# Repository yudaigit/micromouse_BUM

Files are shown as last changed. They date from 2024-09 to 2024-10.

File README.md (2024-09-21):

# Micromouse "BUM"
Contains micromouse specification, code, and list of items.

# Table of Contents
1. Introduction
2. Design Goals
3. Schematic diagram
4. Parts List
5. Codes

# 1. Introduction
**Micromouse** : A maze-solving robot with wall sensors and electric motor.

**Expected specification of this mouse**
- Motor: Stepping Motor (for ease of coding)
- Microcontroller: ESP32
- Wall detection: IR LED + suitable phototransistor
- Wheels: 2 wheels + sheet with smooth surface in front
- Battery: Lipo battery (12V)
- Maze-solving algorism Adachi method
- Chassis would be made out of circuit board. 

**Important Regulation** 
- Mouse must fit on 18cm x 18cm unit square.
- Each run that in which the mouse successfully reaches the goal is given a run time.
- Shortest time out of all runs is considered the official record. 
- 10 minutes limit including adjusting parameters.
- No limit on the number of runs
Regulation found here [2024 IEEE MIT Micromouse Guideline.pdf](https://github.com/user-attachments/files/17085412/2024.IEEE.MIT.Micromouse.Guideline.pdf)

Micromouse_maze
Picture from Wikipedia [Link](https://en.wikipedia.org/wiki/Micromouse)

# 2. Design Goals
Design of this mouse is referred to Beginner Mouse V2 by Micromouse Hokuriku Dokokai. 

Website Link: [Click here](https://sites.google.com/a/itolab-ktc.com/mouse_hokuriku/basicmouse2) 
Website in Japanese so needs Google Translation
初心者マウス二式
Picture from linked website by Micromouse Hokuriku Dokokai

**Changes to be made:**
- Microcontroller changed from RX220 to ESP32S3-devkit
- IR LED and Photo-transistor changed due to item availablity in the US
- Wheels will be manufactured using CNC mills.
- Further modification expected.

# 3. Schematic Diagram
Updated Sep 21 2024
[Schematic Diagram V1.pdf](https://github.com/user-attachments/files/17085267/Schematic.Diagram.V1.pdf)
**Explanation for V1**
- Circuit around motor-driver is set.
- Circuit around power-control is set.
- Needs modification for pin configuratino around ESP32
- Needs modification for buttons.

# 4. Parts List
| Parts Name | Part Number | Website | Explanation |
| --- | --- | --- | --- |
| Microcontroller | ESP32-S3-DEVKITC-1-N8R8 | [Link: Digikey](https://www.digikey.com/en/products/detail/espressif-systems/ESP32-S3-DEVKITC-1-N8R8/15295894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) | Devkit includes USB-UART bridge, Reset/Boot-mode bottons, LDO regulator, micro-USB connector. |
| Motor Driver  | A3982SLBTR-T | [Link: Digikey](https://www.digikey.com/en/products/detail/allegro-microsystems/A3982SLBTR-T/1006337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) | Output drive capacity of up to 35 V and ±2 A |
| Transistor Array  | TBD62083AFNG,EL  | [Link: Digikey](https://www.digikey.com/en/products/detail/toshiba-semiconductor-and-storage/TBD62083AFNG-EL/5514101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) |
| IR LED | SFH 4545 | [Link: Digikey](https://www.digikey.com/en/products/detail/ams-osram-usa-inc/SFH-4545/2205955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) | Peak Wavelength of 950nm. |
| Phototransistor | TEFT4300 | [Link: Digikey](https://www.digikey.com/en/products/detail/vishay-semiconductor-opto-division/TEFT4300/1681175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) | Full performance at wavelength of 940nm |
| Motor | PKP213D05A | [Link: MISUMI](https://us.misumi-ec.com/vona2/detail/221004949472/?HissuCode=PKP213D05A) | Rated Voltage of 4.25V and rated current of 0.5A |
| Regulator | NJM2845DL1-05 | [Link: MOUSER](https://www.mouser.com/ProductDetail/Nisshinbo/NJM2845DL1-05-TE1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) | Converts 12V to 5V |
| Regulator | NJM2845DL1-33 | [Link: MOUSER](https://www.mouser.com/ProductDetail/Nisshinbo/NJM2845DL1-33-TE1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) | Converts 5V to 3.3V |
| Variable Resistor | 3362P-1-103LF | [Link: MOUSER](https://www.mouser.com/ProductDetail/Bourns/3362P-1-103LF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) |

# 5. Codes
Codes were taken and based on Pi:Co V2 Micromouse developed by RT.corp.
Github repo for Pi:Co V2 is found here. [Link](https://github.com/rt-net/pico_v2_arduino_examples)

Explanation of code V1:
- Codes are mostly similar to the one made for Pi:Co V2.
- Some codes were added for better performance, including slalom, hardware correction and wall-cut correction.
- Instead of pushing the button to start, it starts when you wipe a hand in front of the wall-sensor.
- All values were taken for half-size micromouse. For this competition, they must be changed.

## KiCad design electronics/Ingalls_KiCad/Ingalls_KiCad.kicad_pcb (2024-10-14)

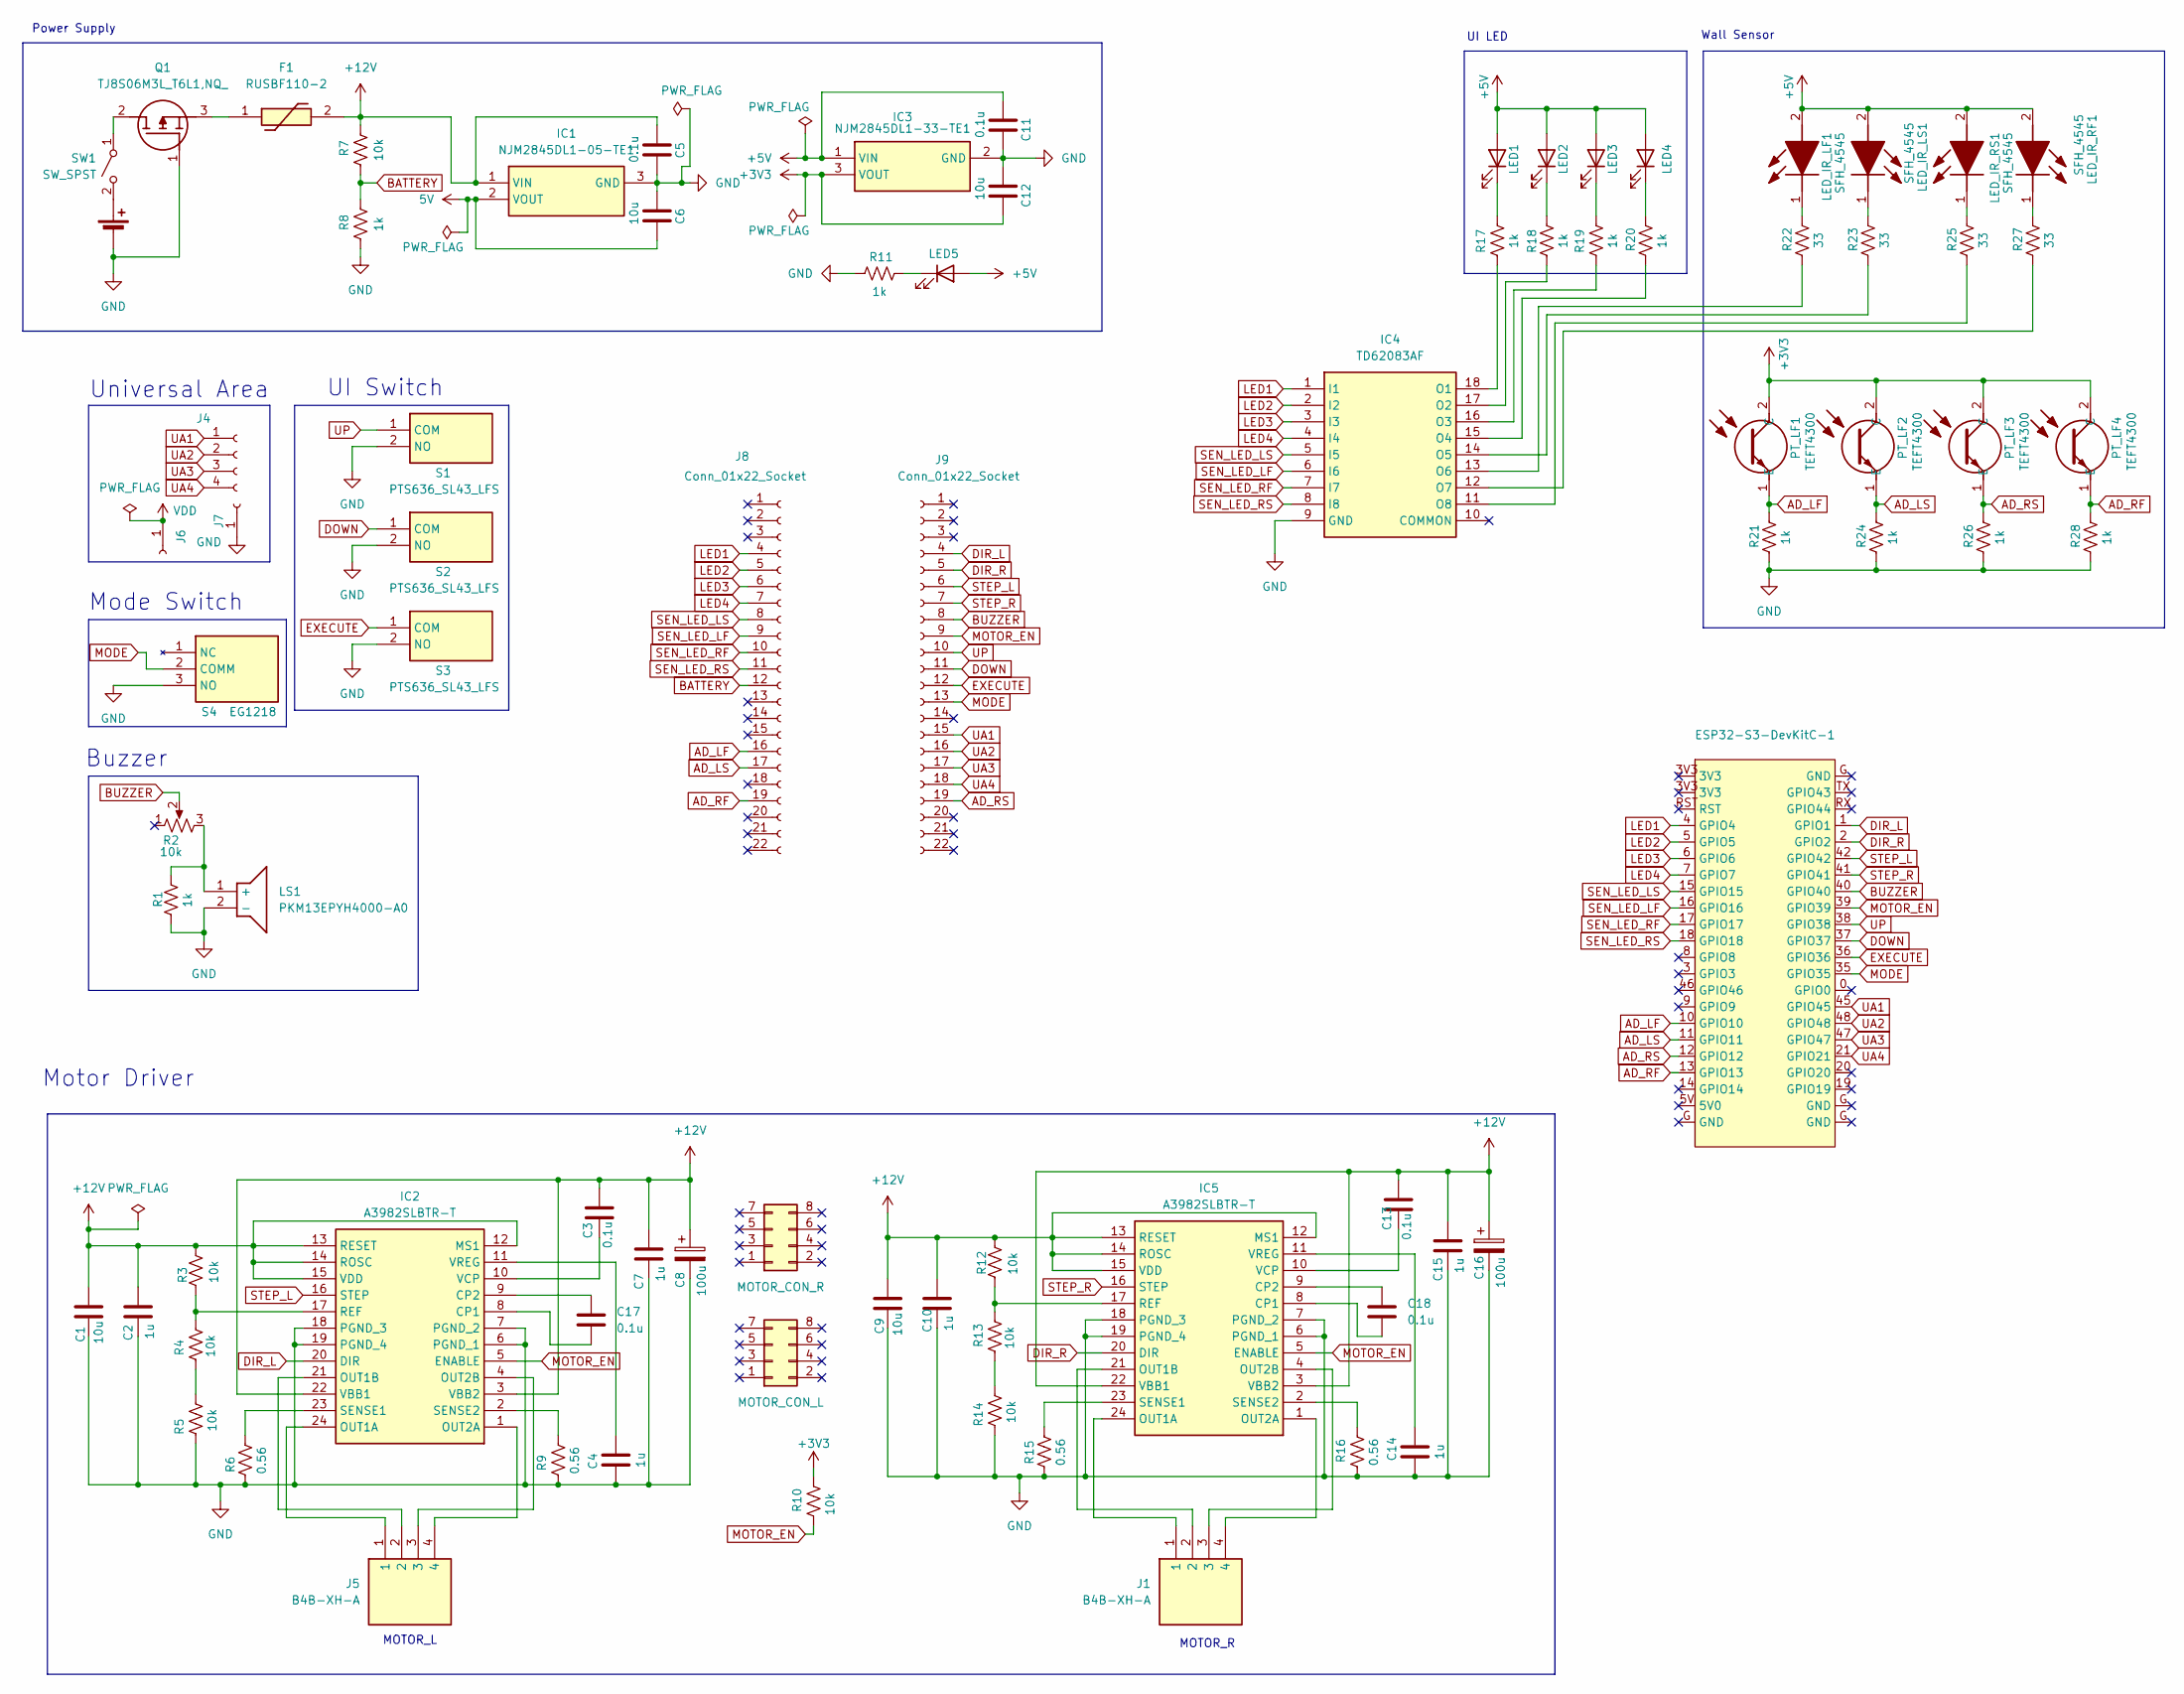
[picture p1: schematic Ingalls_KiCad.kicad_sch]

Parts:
BT1: Battery_Cell; PinHeader_1x02_P1.27mm_Vertical
C1, C6, C9, C12: 10u; C_0603_1608Metric
C2, C4, C7, C10, C14, C15: 1u; C_0603_1608Metric
C3, C5, C11, C13, C17, C18: 0.1u; C_0603_1608Metric
C8, C16: 100u; PCAP_SEP_C6_PAN
D1: LED5; LED_D5.0mm
ESP32-S3-DevKitC-1: (no value)
F1: RUSBF110-2; RUSBF1102; Manufacturer_Part_Number RUSBF110-2; Mouser Part Number 650-RUSBF110-2
IC1: NJM2845DL1-05-TE1; TO-252-3-L1; Manufacturer_Part_Number NJM2845DL1-05-TE1; Mouser Part Number 513-NJM2845DL105-TE1
IC2, IC5: A3982SLBTR-T; A3959SLBTRT; Manufacturer_Part_Number A3982SLBTR-T; Mouser Part Number 250-A3982SLBTR-T
IC3: NJM2845DL1-33-TE1; NJM2845DL133TE1; Manufacturer_Part_Number NJM2845DL1-33-TE1; Mouser Part Number 513-NJM2845DL133-TE1
IC4: TD62083AF; SOIC127P1030X245-18N; Manufacturer_Part_Number TD62083AF
J1, J5: B4B-XH-A; B4BXHA; Manufacturer_Part_Number B4B-XH-A
J2: MOTOR_CON_R
J3: MOTOR_CON_L
J4: Conn_01x04_Socket; PinHeader_1x04_P2.54mm_Vertical
J6, J7: Conn_01x01_Socket; PinSocket_1x01_P2.54mm_Vertical
J8, J9: Conn_01x22_Socket; PinSocket_1x22_P2.54mm_Vertical
LED1, LED2, LED3, LED4: LED; LED_D5.0mm
LED_IR_LF1: SFH_4545; SFH4545; Mouser Part Number 720-SFH4545
LED_IR_LS1: SFH_4545; SFH4545; Mouser Part Number 720-SFH4545
LED_IR_RF1: SFH_4545; SFH4545; Mouser Part Number 720-SFH4545
LED_IR_RS1: SFH_4545; SFH4545; Mouser Part Number 720-SFH4545
LS1: PKM13EPYH4000-A0; PKM13EPYH4000A0; Manufacturer_Part_Number PKM13EPYH4000-A0; Mouser Part Number 81-PKM13EPYH4000-A0
PT_LF1, PT_LF2, PT_LF3, PT_LF4: TEFT4300; Manufacturer_Part_Number TEFT4300; Mouser Part Number 782-TEFT4300
Q1: TJ8S06M3L_T6L1,NQ_; TJ8S06M3LT6L1NQ; Manufacturer_Part_Number TJ8S06M3L(T6L1,NQ); Mouser Part Number 757-TJ8S06M3LT6L1NQ
R1, R8, R11, R17, R18, R19, R20, R21, R24, R26, R28: 1k; R_0603_1608Metric
R2: 10k; 3362P_1
R3, R4, R5, R7, R10, R12, R13, R14: 10k; R_0603_1608Metric
R6, R9, R15, R16: 0.56; R_2512_6332Metric
R22, R23, R25, R27: 33; R_0603_1608Metric
S1, S2, S3: PTS636_SL43_LFS; PTS636SL43LFS; Manufacturer_Part_Number PTS636 SL43 LFS; Mouser Part Number 611-PTS636SL43LFS
S4: EG1218; SW_1218_EWI; Manufacturer_Part_Number EG1218; Mouser Part Number 612-EG1218
SW1: SW_SPST; ANT11SF1CQE

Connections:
5V: C6.1, IC1.2 (VOUT)
+3V3: C12.1, IC3.3 (VOUT), PT_LF1.2 (C), PT_LF2.2 (C), PT_LF3.2 (C), PT_LF4.2 (C), R10.1
+5V: C11.2, D1.2 (A), IC3.1 (VIN), LED1.2 (A), LED2.2 (A), LED3.2 (A), LED4.2 (A), LED_IR_LF1.2 (A), LED_IR_LS1.2 (A), LED_IR_RF1.2 (A), LED_IR_RS1.2 (A)
+12V: C1.1, C2.1, C3.1, C5.2, C7.1, C8.1, C9.1, C10.1, C13.1, C15.1, C16.1, F1.2, IC1.1 (VIN), IC2.3 (VBB2), IC2.12 (MS1), IC2.13 (RESET), IC2.14 (ROSC), IC2.15 (VDD), IC2.22 (VBB1), IC5.3 (VBB2), IC5.12 (MS1), IC5.13 (RESET), IC5.14 (ROSC), IC5.15 (VDD), IC5.22 (VBB1), R3.1, R7.2, R12.1
AD_LF: ESP32-S3-DevKitC-1.10 (GPIO10), J8.16, PT_LF1.1 (E), R21.1
AD_LS: ESP32-S3-DevKitC-1.11 (GPIO11), J8.17, PT_LF2.1 (E), R24.1
AD_RF: ESP32-S3-DevKitC-1.13 (GPIO13), J8.19, PT_LF4.1 (E), R28.1
AD_RS: ESP32-S3-DevKitC-1.12 (GPIO12), J9.19, PT_LF3.1 (E), R26.1
BATTERY: J8.12, R7.1, R8.2
BUZZER: ESP32-S3-DevKitC-1.40 (GPIO40), J9.8, R2.2
DIR_L: ESP32-S3-DevKitC-1.1 (GPIO1), IC2.20 (DIR), J9.4
DIR_R: ESP32-S3-DevKitC-1.2 (GPIO2), IC5.20 (DIR), J9.5
DOWN: ESP32-S3-DevKitC-1.37 (GPIO37), J9.11, S2.1 (COM)
EXECUTE: ESP32-S3-DevKitC-1.36 (GPIO36), J9.12, S3.1 (COM)
GND: BT1.2 (-), C1.2, C2.2, C4.2, C5.1, C6.2, C7.2, C8.2, C9.2, C10.2, C11.1, C12.2, C14.2, C15.2, C16.2, IC1.3 (GND), IC2.6 (PGND_1), IC2.7 (PGND_2), IC2.18 (PGND_3), IC2.19 (PGND_4), IC3.2 (GND), IC4.9 (GND), IC5.6 (PGND_1), IC5.7 (PGND_2), IC5.18 (PGND_3), IC5.19 (PGND_4), J7.1, LS1.2 (-), Q1.1 (G), R1.2, R5.2, R6.2, R8.1, R9.2, R11.1, R14.2, R15.2, R16.2, R21.2, R24.2, R26.2, R28.2, S1.2 (NO), S2.2 (NO), S3.2 (NO), S4.3 (NO); also elsewhere on the board
LED1: ESP32-S3-DevKitC-1.4 (GPIO4), IC4.1 (I1), J8.4
LED2: ESP32-S3-DevKitC-1.5 (GPIO5), IC4.2 (I2), J8.5
LED3: ESP32-S3-DevKitC-1.6 (GPIO6), IC4.3 (I3), J8.6
LED4: ESP32-S3-DevKitC-1.7 (GPIO7), IC4.4 (I4), J8.7
MODE: ESP32-S3-DevKitC-1.35 (GPIO35), J9.13, S4.2 (COMM); also elsewhere on the board
MOTOR_EN: ESP32-S3-DevKitC-1.39 (GPIO39), IC2.5 (ENABLE), IC5.5 (ENABLE), J9.9, R10.2
unnamed: BT1.1 (+), SW1.2 (B)
unnamed: D1.1 (K), R11.2
unnamed: C17.2, IC2.8 (CP1)
unnamed: C17.1, IC2.9 (CP2)
unnamed: IC2.24 (OUT1A), J5.1
unnamed: IC2.21 (OUT1B), J5.2
unnamed: IC2.1 (OUT2A), J5.4
unnamed: IC2.4 (OUT2B), J5.3
unnamed: IC2.17 (REF), R3.2, R4.1
unnamed: IC2.23 (SENSE1), R6.1
unnamed: IC2.2 (SENSE2), R9.1
unnamed: C3.2, IC2.10 (VCP)
unnamed: C4.1, IC2.11 (VREG)
unnamed: IC4.18 (O1), R17.2
unnamed: IC4.17 (O2), R18.2
unnamed: IC4.16 (O3), R19.2
unnamed: IC4.15 (O4), R20.2
unnamed: IC4.14 (O5), R23.2
unnamed: IC4.13 (O6), R22.2
unnamed: IC4.12 (O7), R27.2
unnamed: IC4.11 (O8), R25.2
unnamed: C18.2, IC5.8 (CP1)
unnamed: C18.1, IC5.9 (CP2)
unnamed: IC5.24 (OUT1A), J1.1
unnamed: IC5.21 (OUT1B), J1.2
unnamed: IC5.1 (OUT2A), J1.4
unnamed: IC5.4 (OUT2B), J1.3
unnamed: IC5.17 (REF), R12.2, R13.1
unnamed: IC5.23 (SENSE1), R15.1
unnamed: IC5.2 (SENSE2), R16.1
unnamed: C13.2, IC5.10 (VCP)
unnamed: C14.1, IC5.11 (VREG)
unnamed: LED1.1 (K), R17.1
unnamed: LED2.1 (K), R18.1
unnamed: LED3.1 (K), R19.1
unnamed: LED4.1 (K), R20.1
unnamed: LED_IR_LF1.1 (K), R22.1
unnamed: LED_IR_LS1.1 (K), R23.1
unnamed: LED_IR_RF1.1 (K), R27.1
unnamed: LED_IR_RS1.1 (K), R25.1
unnamed: LS1.1 (+), R1.1, R2.3
unnamed: Q1.2 (D), SW1.1 (A)
unnamed: F1.1, Q1.3 (S)
unnamed: R4.2, R5.1
unnamed: R13.2, R14.1
SEN_LED_LF: ESP32-S3-DevKitC-1.16 (GPIO16), IC4.6 (I6), J8.9
SEN_LED_LS: ESP32-S3-DevKitC-1.15 (GPIO15), IC4.5 (I5), J8.8
SEN_LED_RF: ESP32-S3-DevKitC-1.17 (GPIO17), IC4.7 (I7), J8.10
SEN_LED_RS: ESP32-S3-DevKitC-1.18 (GPIO18), IC4.8 (I8), J8.11
STEP_L: ESP32-S3-DevKitC-1.42 (GPIO42), IC2.16 (STEP), J9.6
STEP_R: ESP32-S3-DevKitC-1.41 (GPIO41), IC5.16 (STEP), J9.7
UA1: ESP32-S3-DevKitC-1.45 (GPIO45), J4.1, J9.15
UA2: ESP32-S3-DevKitC-1.48 (GPIO48), J4.2, J9.16
UA3: ESP32-S3-DevKitC-1.47 (GPIO47), J4.3, J9.17
UA4: ESP32-S3-DevKitC-1.21 (GPIO21), J4.4, J9.18
UP: ESP32-S3-DevKitC-1.38 (GPIO38), J9.10, S1.1 (COM)
VDD: J6.1

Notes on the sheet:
UI Switch
Buzzer
Mode Switch
Wall Sensor
Universal Area
MOTOR_L
MOTOR_R
Motor Driver
Power Supply
UI LED

Board: 2 copper layers, 80 parts (0 on the bottom side), 77 nets, no tracks yet.

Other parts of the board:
SW_MODE1: SW_1218_EWI

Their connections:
GND: SW_MODE1.2 (B); also elsewhere on the board
MODE: SW_MODE1.1 (C); also elsewhere on the board

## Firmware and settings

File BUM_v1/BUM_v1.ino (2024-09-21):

// Copyright 2023 RT Corporation
//
// Licensed under the Apache License, Version 2.0 (the "License");
// you may not use this file except in compliance with the License.
// You may obtain a copy of the License at
//
//     http://www.apache.org/licenses/LICENSE-2.0
//
// Unless required by applicable law or agreed to in writing, software
// distributed under the License is distributed on an "AS IS" BASIS,
// WITHOUT WARRANTIES OR CONDITIONS OF ANY KIND, either express or implied.
// See the License for the specific language governing permissions and
// limitations under the License.

#include "FS.h"
#include "SPIFFS.h"
#include "device.h"
#include "map_manager.h"
#include "mytypedef.h"
#include "parameter.h"

signed char g_mode;
short g_battery_value;
t_sensor g_sen_r, g_sen_l, g_sen_fr, g_sen_fl;
t_control g_con_wall;

float r_adjust_len = 0.0, l_adjust_len = 0.0;

volatile double g_accel_r;
volatile double g_accel_l;
double g_max_speed_r, g_max_speed_l, g_min_speed_r, g_min_speed_l;
volatile double g_speed_r;
volatile double g_speed_l;
volatile bool g_motor_move;
MapManager g_map_control;

void setup()
{
  // put your setup code here, to run once:

  initAll();
  disableBuzzer();
  g_mode = 1;
}

void loop()
{
  int run_modes[] = {1, 2, 3, 4, 5, 6, 7, 8, 9, 10, 11, 12, 13, 14}; // 1から3の走行モードを指定

  setLED(g_mode);
  switch (getSW()) {
    case SW_RM: // 右のボタンが押された時
      g_mode = incButton(g_mode, 15, 1);
      break;
    case SW_LM: // 左のボタンが押された時
      okButton(); // ブザーを鳴らす
      for (int run_mode : run_modes){
        if (g_mode == run_mode) {
          enableMotor();
          detect_hand();
          okButton();
        }
      }
      execByMode(g_mode);
      break;
  }
  delay(1);
}

void execByMode(int mode)
{
  delay(1000);

  switch (mode) {
    case 1:
      searchLefthand();
      break;
    case 2:  //足立法
      g_map_control.positionInit();
      searchAdachi(g_map_control.getGoalX(), g_map_control.getGoalY());
      rotate(right, 2);
      g_map_control.nextDir(right);
      g_map_control.nextDir(right);
      goalAppeal();
      searchAdachi(0, 0);
      rotate(right, 2);
      g_map_control.nextDir(right);
      g_map_control.nextDir(right);
      mapWrite();
      break;
    case 3:  //最短走行
      copyMap();
      g_map_control.positionInit();
      fastRun1(g_map_control.getGoalX(), g_map_control.getGoalY());
      rotate(right, 2);
      g_map_control.nextDir(right);
      g_map_control.nextDir(right);
      goalAppeal();
      fastRun1(0, 0);
      rotate(right, 2);
      g_map_control.nextDir(right);
      g_map_control.nextDir(right);
      break;
    case 4:
      copyMap();
      g_map_control.positionInit();
      fastRun2(g_map_control.getGoalX(), g_map_control.getGoalY());
      rotate(right, 2);
      g_map_control.nextDir(right);
      g_map_control.nextDir(right);
      goalAppeal();
      fastRun2(0, 0);
      rotate(right, 2);
      g_map_control.nextDir(right);
      g_map_control.nextDir(right);
      break;
    case 5:
      break;
    case 6:
      break;
    case 7:
      break;
    case 8:
      break;
    case 9:
      break;
    case 10:
      break;
    case 11:
      break;
    case 12:
      break;
    case 13:
      break;
    case 14:
      break;
    case 15:
      disableMotor();
      adjustMenu();  //調整メニューに行く
      break;
    default:
      break;
  }
  disableMotor();
}

void detect_hand(void) {
  int count = 0;
  const int TH_DETECT_FR = 700;
  const int TH_DETECT_FL = 900;

  while(count <= 5){
    if (g_sen_fr.value > TH_DETECT_FR || g_sen_fl.value > TH_DETECT_FL){
      count++;
      delay(100);
    //}
    delay(10);
  }
}
}

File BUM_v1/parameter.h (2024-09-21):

#ifndef PARAMETER_H_
#define PARAMETER_H_

#define TIRE_DIAMETER (24.7)
#define TREAD_WIDTH (30.4)
#define TREAD_CIRCUIT (TREAD_WIDTH * PI / 4)
#define PULSE (TIRE_DIAMETER * PI / (35.0 / 10.0 * 20.0 * 8.0))
#define MIN_HZ 40

#define WAITLOOP_SLED 10

#define REF_SEN_R 370
#define REF_SEN_L 460

#define TH_SEN_R 128
#define TH_SEN_L 143
#define TH_SEN_FR 152
#define TH_SEN_FL 176

#define CONTROL_TH_SEN_R TH_SEN_R
#define CONTROL_TH_SEN_L TH_SEN_L

#define CON_WALL_KP 0.12 // 0.12
#define SEARCH_ACCEL 1.5
#define TURN_ACCEL 0.3
#define HOSEI_ACCEL 0.3
#define HOSEI_SPEED 50

#define SEARCH_SPEED 200
#define MAX_SPEED 600
#define MIN_SPEED (MIN_HZ * PULSE)

#define GOAL_X 4
#define GOAL_Y 4

#define INC_FREQ 3000
#define DEC_FREQ 2000

#define BATT_MAX 4000
#define BATT_MIN 3800

#define HALF_SECTION 45
#define SECTION 90

#define r_hosei 54.25
#define l_hosei 56.65

#define slalom_speed_longer 301//267
#define slalom_speed_shorter 98
#define slalom_accel_longer 1
#define slalom_accel_shorter -1
const double turnRadius = 36.0;

#endif  // PARAMETER_H_

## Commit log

2024-10-14 Added Ingalls-1GO KiCAD project
    [Ingalls-1GO.kicad_pcb, Ingalls-1GO.kicad_sch]
2024-10-14 Moved KiCAD project files to electronics directory
    [Ingalls-1GO.kicad_pcb, Ingalls-1GO.kicad_sch]
2024-10-14 File name changed
    [Ingalls_KiCad.kicad_pcb, Ingalls_KiCad.kicad_sch]
